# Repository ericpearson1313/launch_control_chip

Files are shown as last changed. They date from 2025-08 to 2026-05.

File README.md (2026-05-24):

# launch_chip
A model rocket launch control chip. A better push button?

## Datasheet
Semiconductors start out as an idea. Early datasheets allow exploration of the functionallity to meet the system need.
I've created a mock datasheet for a launch control chip, to both inspire and try to ground my design as a practical device with multiple applications.
Key functions and parameters set and documented. A compact module was defined which encompassed core functionallity centered around the device. Considering
multiple applications for this module firmed up the I/O to ease integration with clean schematics for each situation. A development board was then designed,
fully integration the LCC into a single board handheld lauch controller, and enabling chip development.

[Datasheet](Launch_chip_arch.pdf)

## Development Board PCB Design
Guided by the datasheet thought process the development board PCB was designed. The KiCad schematic and pcb have been developed and added to the repo.
The design will be revisioned until tapeout release. I'll use this board to bring up the LCC.

[KiCAD Project](dev_board.kicad_pro)

[KiCAD Schematic](dev_board.kicad_sch)

[KiCAD PCB](dev_board.kicad_pcb)

[Bill of Materials](dev_board.csv)

## Datasheet Snapshots

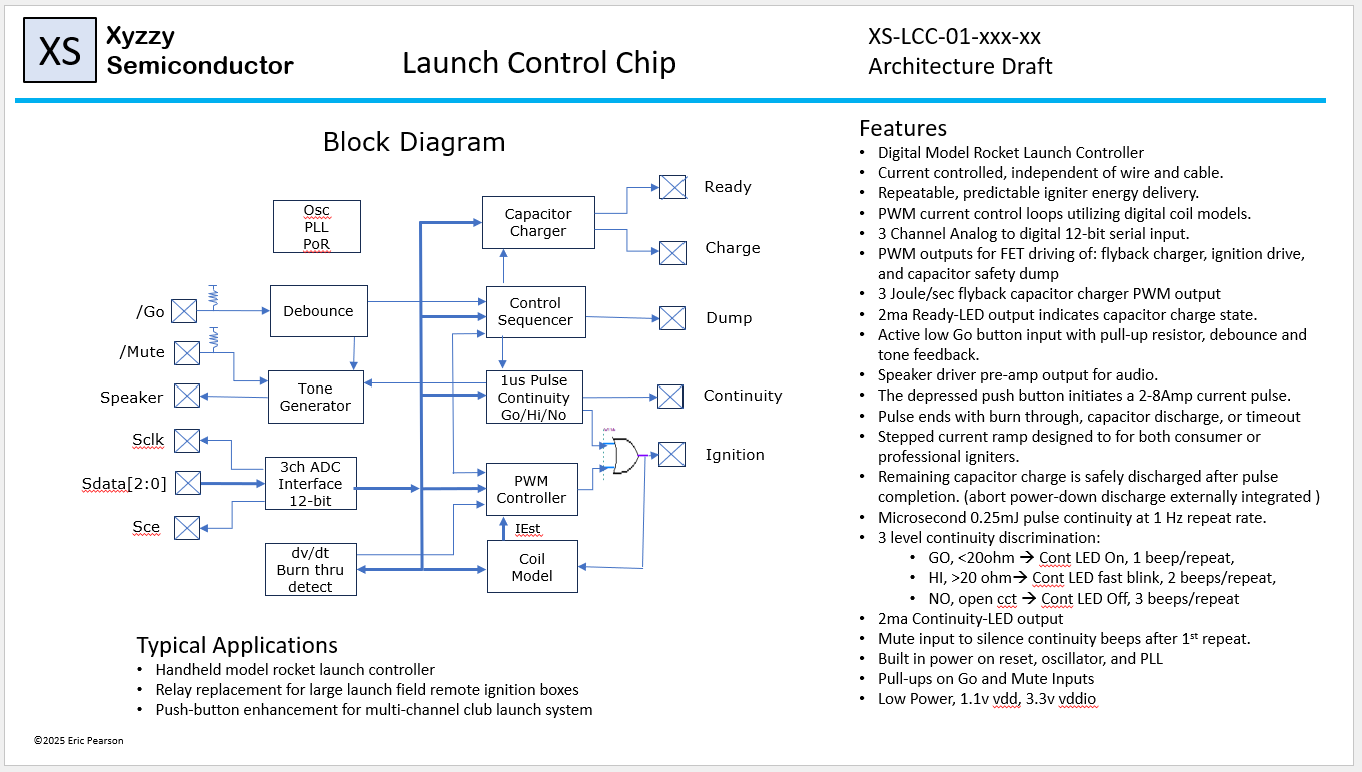
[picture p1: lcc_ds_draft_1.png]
features


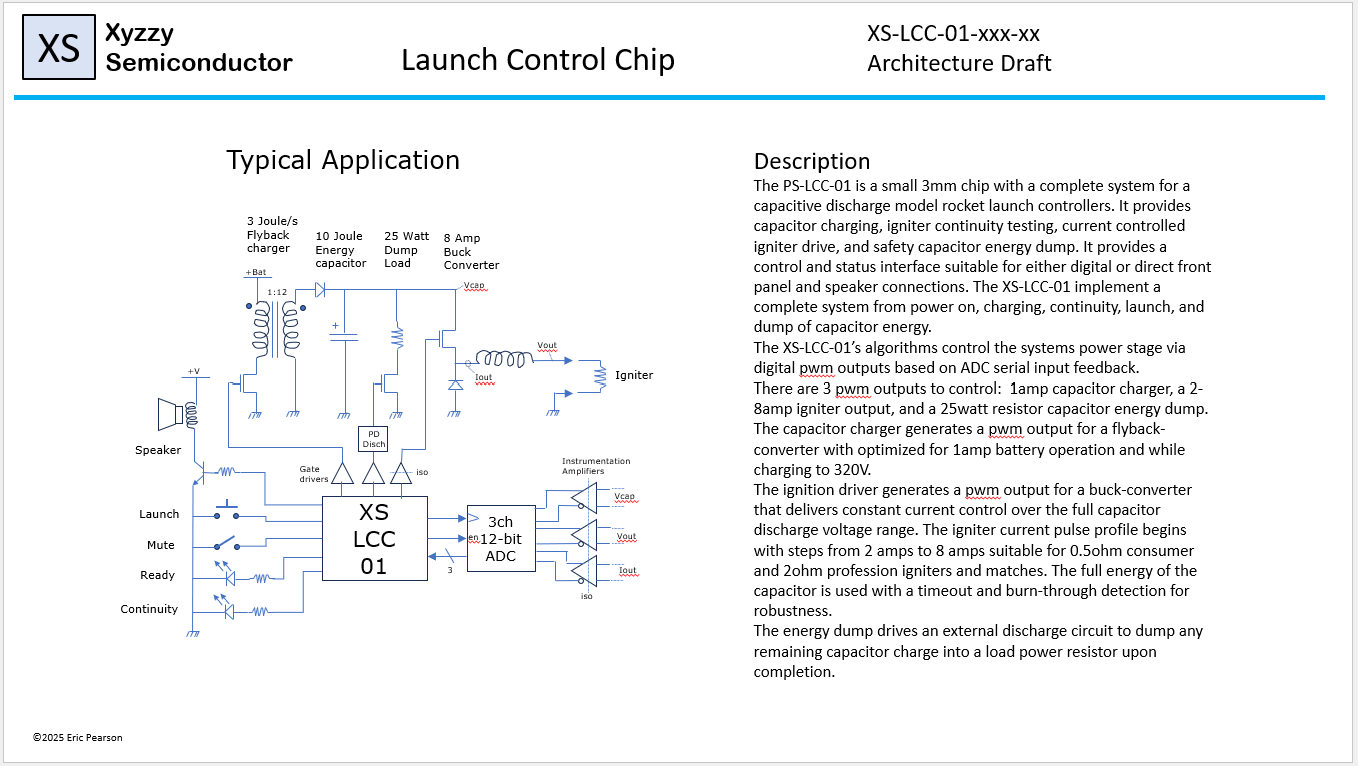
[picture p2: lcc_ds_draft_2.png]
application


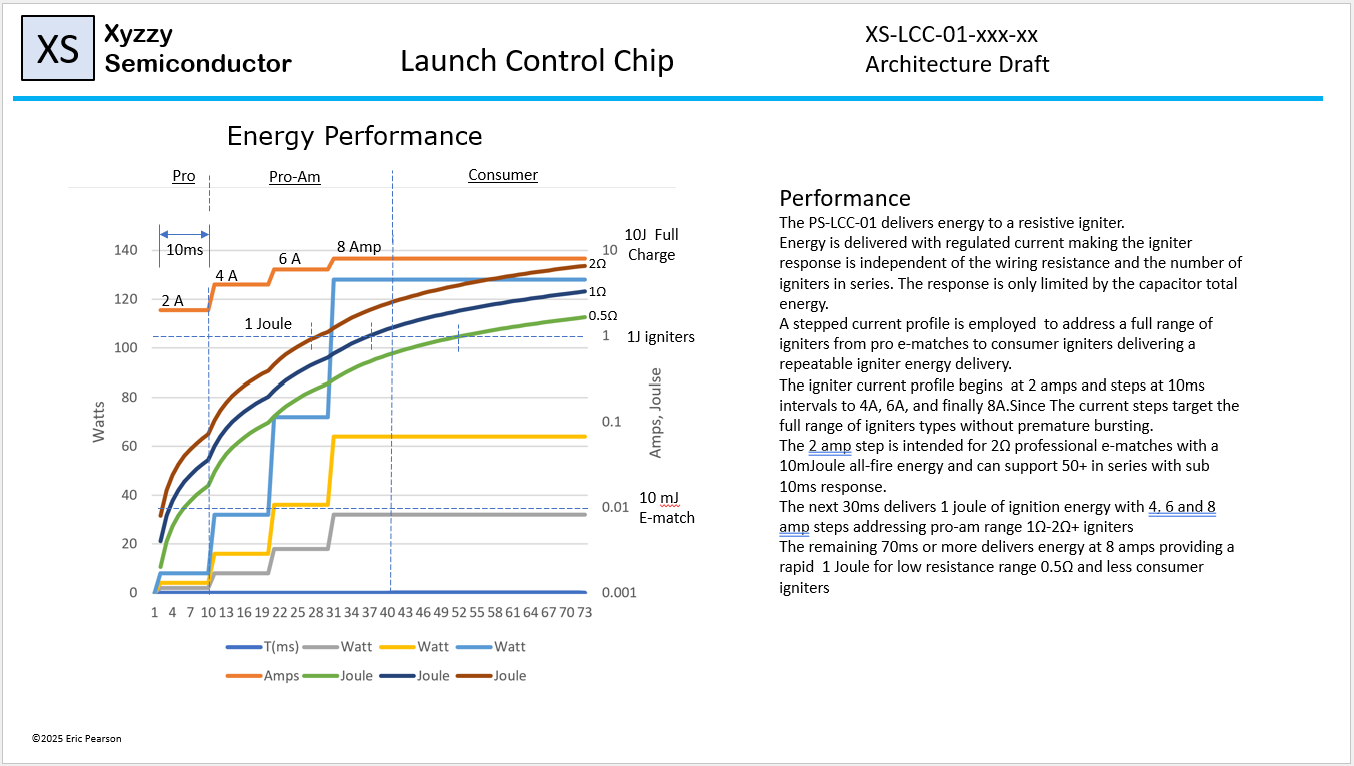
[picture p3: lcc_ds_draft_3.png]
performance


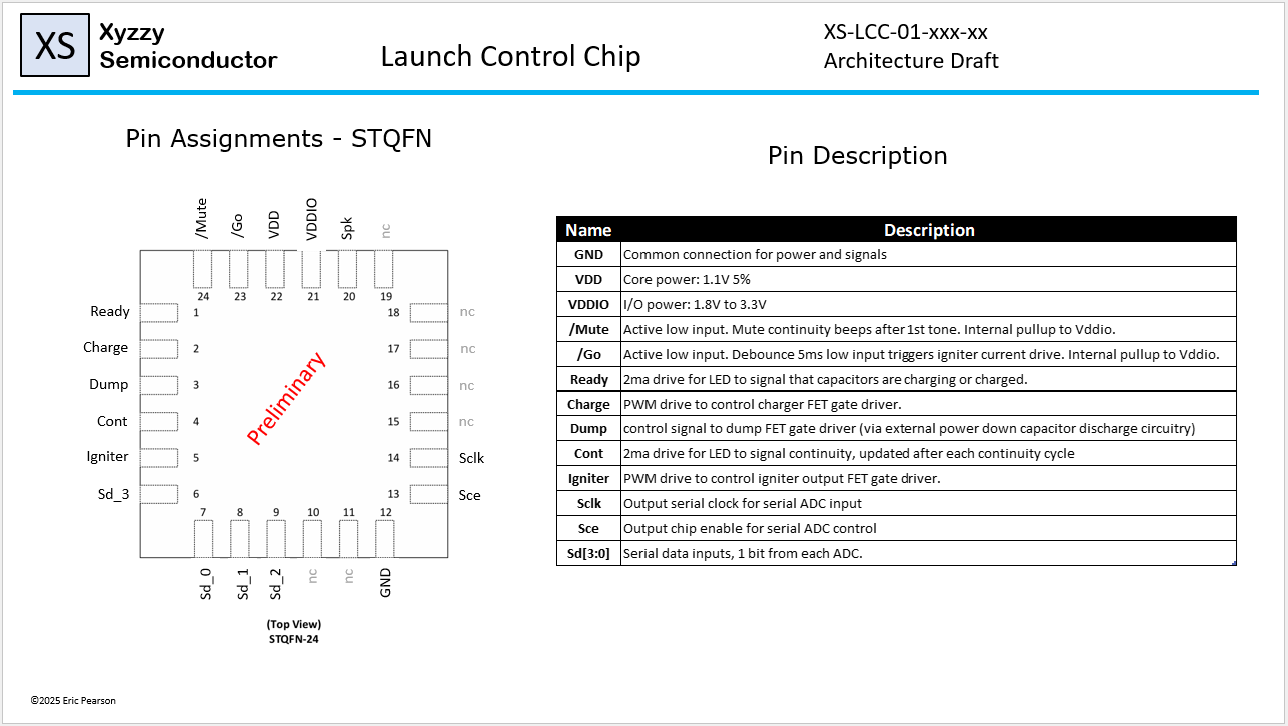
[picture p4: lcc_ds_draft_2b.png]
pinout


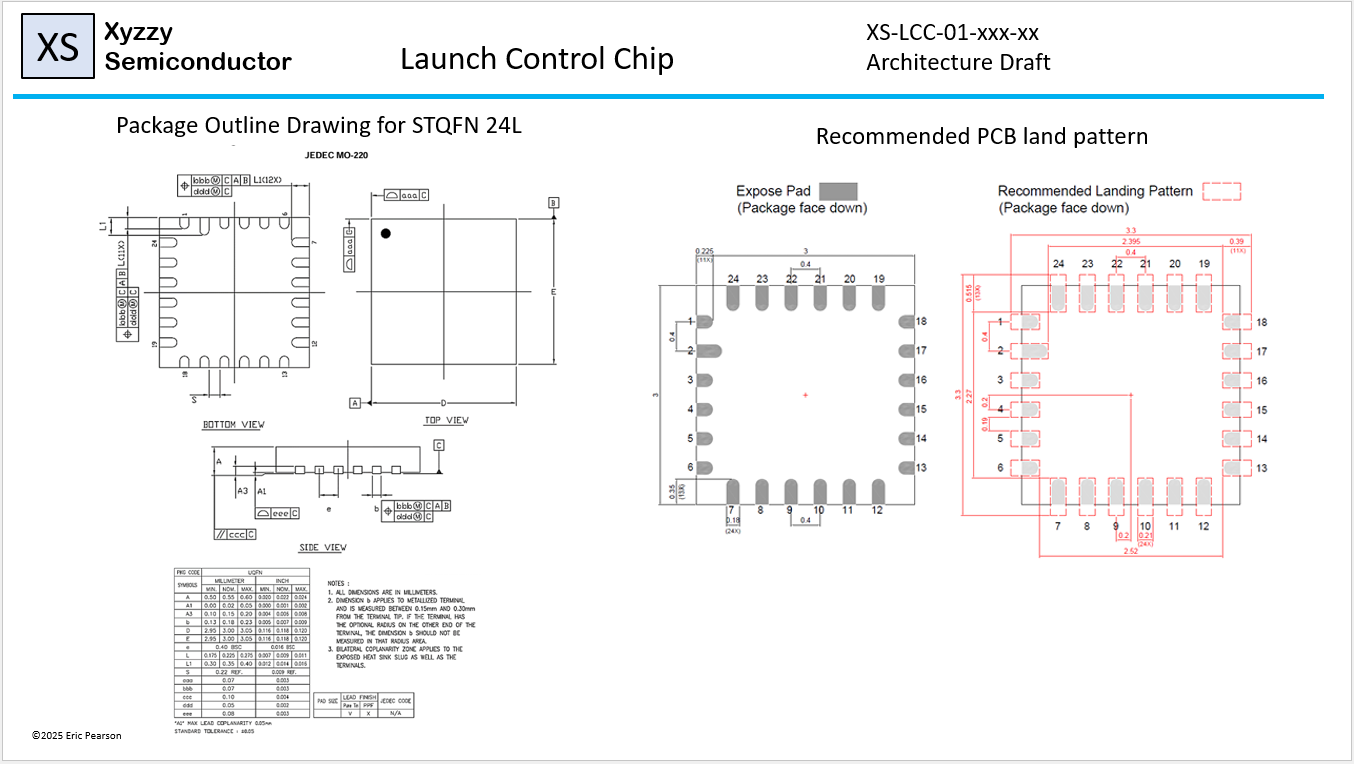
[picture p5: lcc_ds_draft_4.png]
package


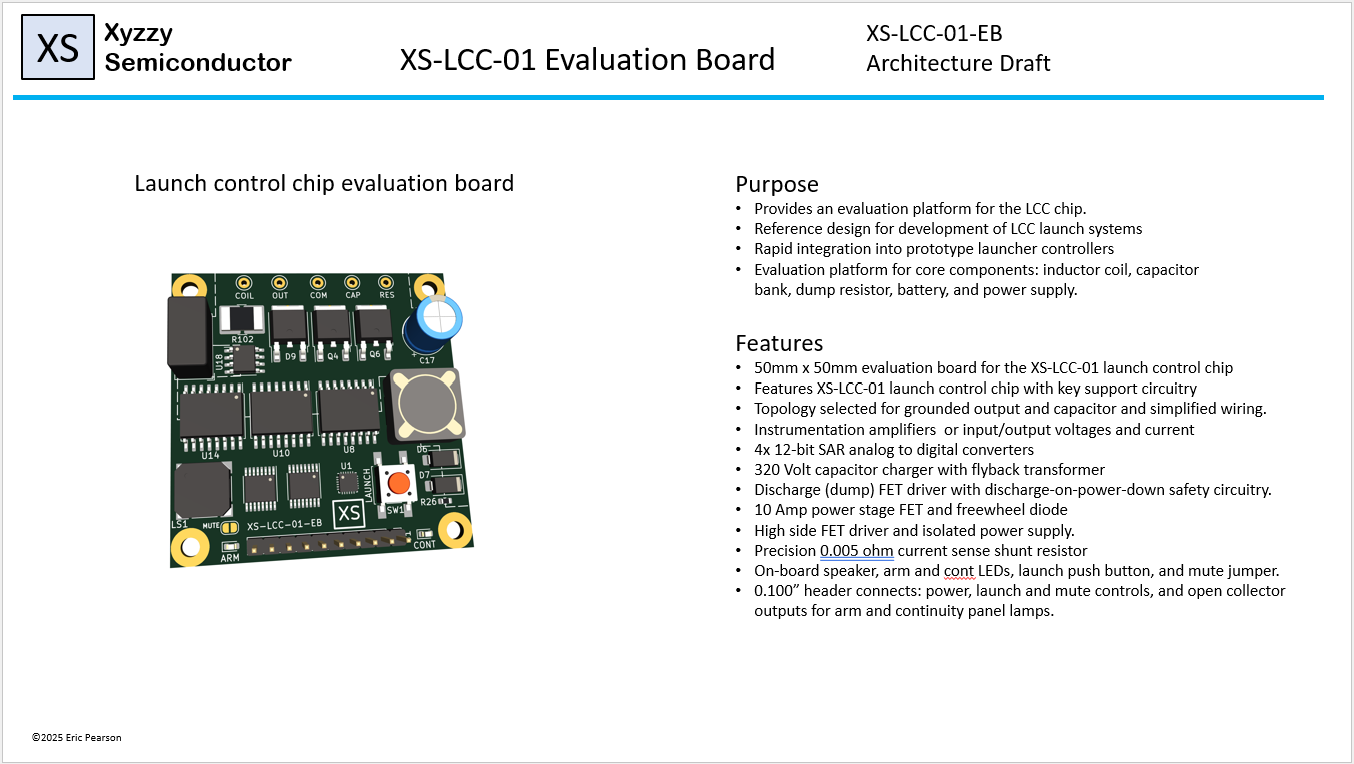
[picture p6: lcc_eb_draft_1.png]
evalboard


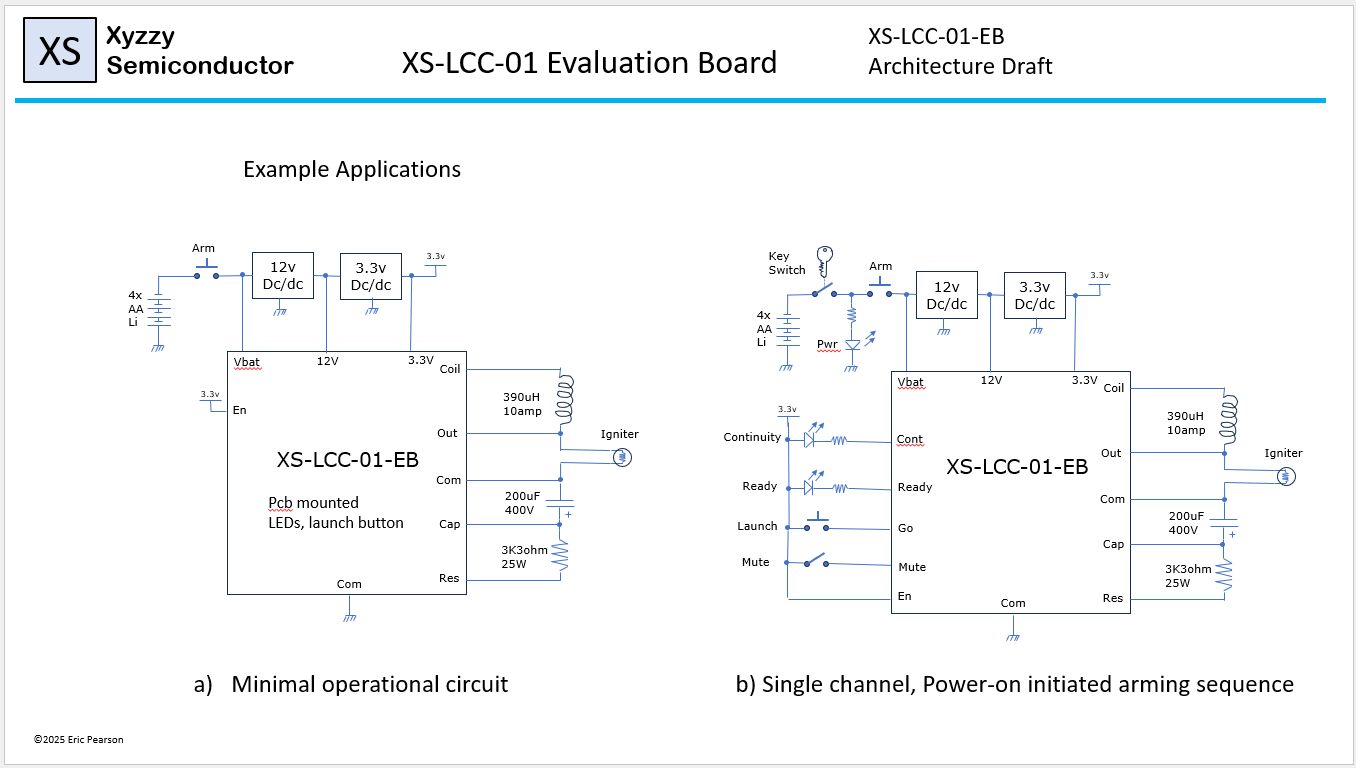
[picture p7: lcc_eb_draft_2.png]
eb_1chan


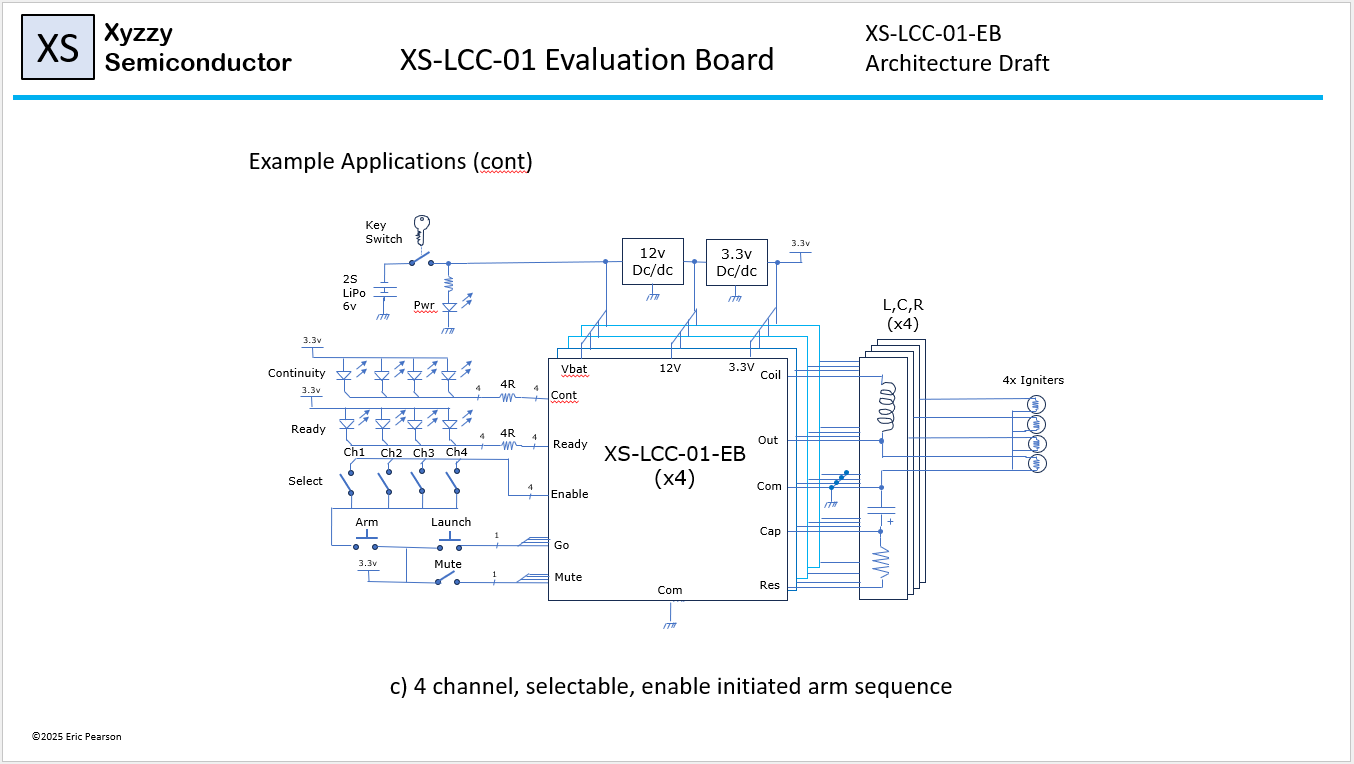
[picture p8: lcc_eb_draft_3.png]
eb_4chan


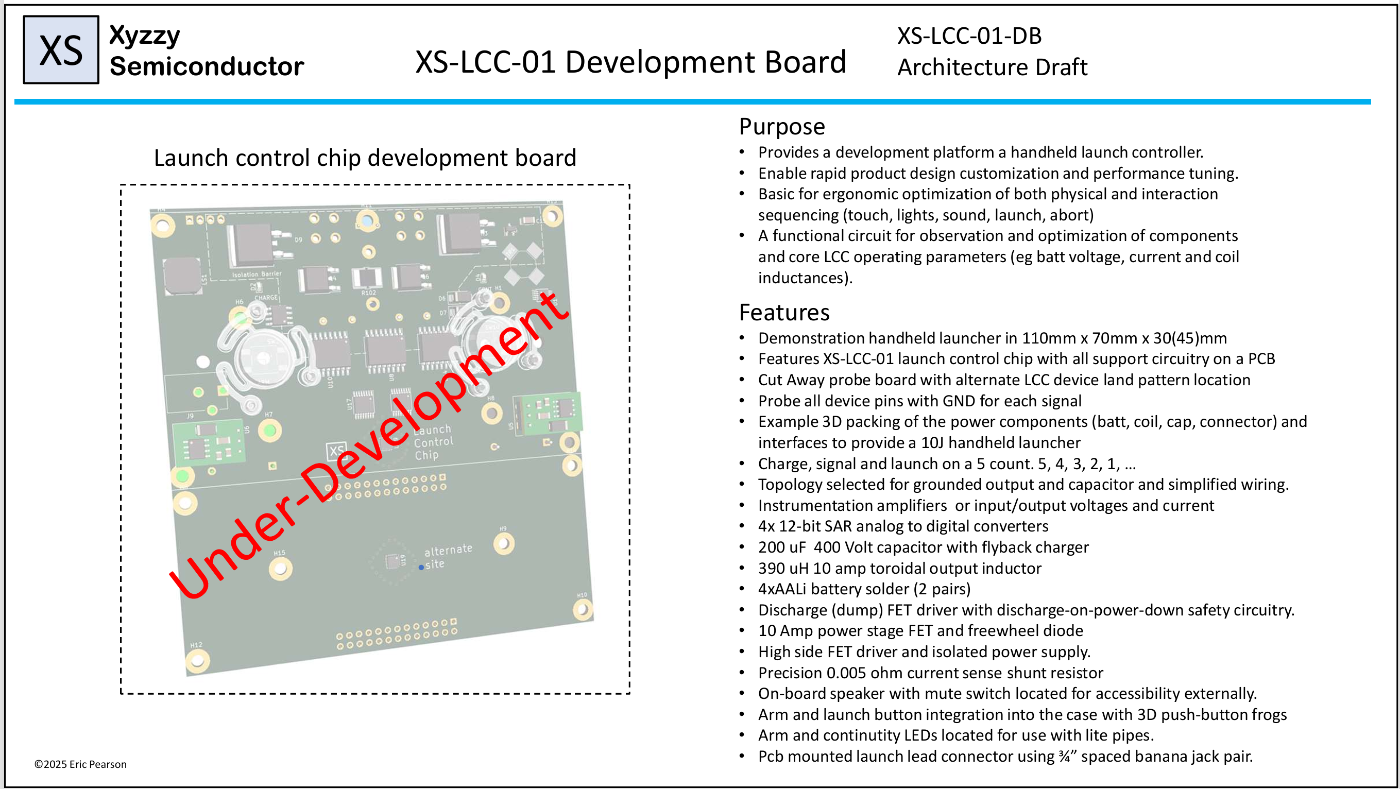
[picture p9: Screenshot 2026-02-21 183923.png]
dev_brd_pre


#### Extra prototype devices 

I have finished development of my 'perfect?' handheld launch controller powered by the launch control chip. Of the prototype run of devices I have a few extra, and have listed them for sale at cost on Ebay for an offer of $35, with free lettermail shipping. If you have followed the same technical direction as myself, I know this chip would have helped me alot, so maybe it could help other similar hobby technical enthusiasts. [LCC-01 Ebay listing](https://www.ebay.ca/itm/157937950540)

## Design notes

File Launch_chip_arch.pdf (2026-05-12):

Osc
PLL
PoR

Coil
Model

PWM
Controller

Ignition

Tone
Generator Speaker | Continuity

Capacitor
Charger

Ready

/Go | Control
Sequencer | Dump

Charge

3ch ADC
Interface
12-bit

Sdata[2:0]

IEst

## Block Diagram

1us Pulse
Continuity
Go/Hi/No

Debounce

dv/dt
Burn thru
detect

/Mute

Sclk

Sce

## Features

- Digital Model Rocket Launch Controller • Current controlled, independent of wire and cable. • Repeatable, predictable igniter energy delivery. • PWM current control loops utilizing digital coil models. • 3 Channel Analog to digital 12-bit serial input. • PWM outputs for FET driving of: flyback charger, ignition drive,

and capacitor safety dump • 3 Joule/sec flyback capacitor charger PWM output • 2ma Ready-LED output indicates capacitor charge state. • Active low Go button input with pull-up resistor, debounce and

tone feedback. • Speaker driver pre-amp output for audio. • The depressed push button initiates a 2-8Amp current pulse. • Pulse ends with burn through, capacitor discharge, or timeout • Stepped current ramp designed to for both consumer or

professional igniters. • Remaining capacitor charge is safely discharged after pulse

completion. (abort power-down discharge externally integrated ) • Microsecond 0.25mJ pulse continuity at 1 Hz repeat rate. • 3 level continuity discrimination: • GO, <20ohm Cont LED On, 1 beep/repeat, • HI, >20 ohm Cont LED fast blink, 2 beeps/repeat, • NO, open cct Cont LED Off, 3 beeps/repeat • 2ma Continuity-LED output • Mute input to silence continuity beeps after 1st repeat. • Built in power on reset, oscillator, and PLL

- Pull-ups on Go and Mute Inputs
- Low Power, 1.1v vdd, 3.3v vddio
- Small size, 3mm x 3mm

## Typical Applications

- Handheld model rocket launch controller • Relay replacement for large launch field remote ignition boxes
- Push-button enhancement for multi-channel club launch system

## Xyzzy

Semiconductor | Launch Control Chip
XS-LCC-01-xxx-xx XS | Architecture Draft

©2025 Eric Pearson

XS

## LCC

01

## +Bat Typical Application

## Xyzzy

# Semiconductor Launch Control Chip

## XS-LCC-01-xxx-xx Architecture Draft 1:12

### 3 Joule/s

Flyback
charger

### 10 Joule

Energy
capacitor

### 25 Watt

Dump
Load

### 8 Amp

Buck
Converter

Igniter

iso Gate drivers

Vcap | Vout Iout Speaker

Launch

Mute

Ready

Continuity

+V

3ch
12-bit
ADC

3

en

iso

Iout Vout Vcap

Instrumentation Amplifiers PD Disch

## Description

The PS-LCC-01 is a small 3mm chip with a complete system for a capacitive discharge model rocket launch controllers. It provides capacitor charging, igniter continuity testing, current controlled igniter drive, and safety capacitor energy dump. It provides a control and status interface suitable for either digital or direct front panel and speaker connections. The XS-LCC-01 implement a complete system from power on, charging, continuity, launch, and dump of capacitor energy.
The XS-LCC-01’s algorithms control the systems power stage via digital pwm outputs based on ADC serial input feedback.
There are 3 pwm outputs to control: 1amp capacitor charger, a 2-8amp igniter output, and a 25watt resistor capacitor energy dump. The capacitor charger generates a pwm output for a flyback-converter with optimized for 1amp battery operation and while charging to 320V.
The ignition driver generates a pwm output for a buck-converter that delivers constant current control over the full capacitor discharge voltage range. The igniter current pulse profile begins with steps from 2 amps to 8 amps suitable for 0.5ohm consumer and 2ohm profession igniters and matches. The full energy of the capacitor is used with a timeout and burn-through detection for robustness.
The energy dump drives an external discharge circuit to dump any remaining capacitor charge into a load power resistor upon completion.

XS

©2025 Eric Pearson

## Xyzzy

# Semiconductor Launch Control Chip

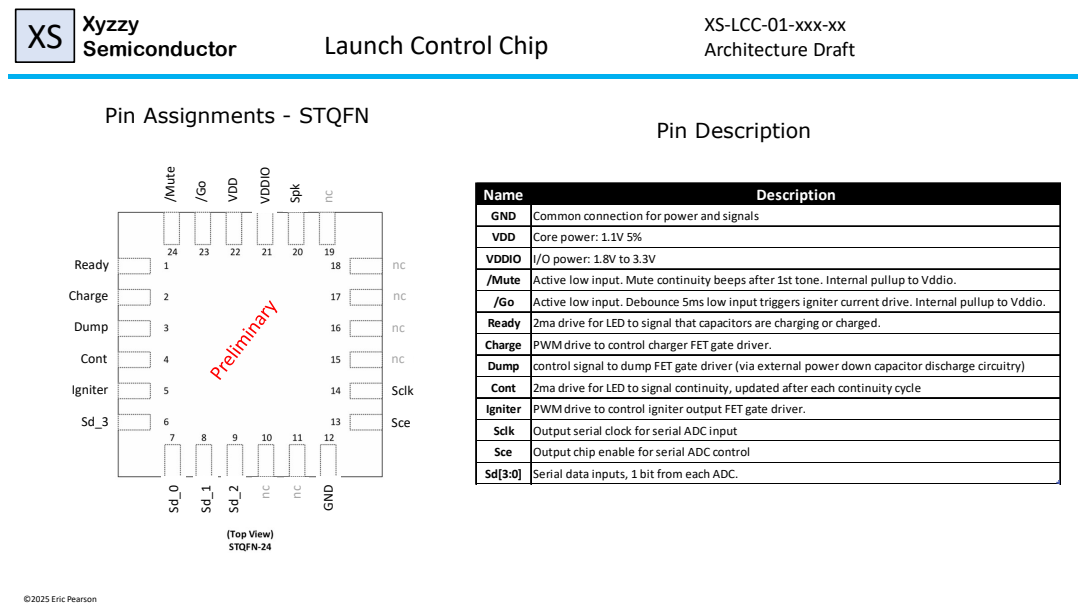
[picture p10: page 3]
XS-LCC-01-xxx-xx XS; Architecture Draft; ©2025 Eric Pearson; VDD; VDDIO; Sclk; Sce; Ready; Charge; Dump; Cont; Igniter; GNDnc; nc /Mute; Spk Sd_0; Pin Description

Pin Assignments - STQFN

Name | Description
GND | Common connection for power and signals
VDD | Core power: 1.1V 5%
VDDIO | I/O power: 1.8V to 3.3V
/Mute | Active low input. Mute continuity beeps after 1st tone. Internal pullup to Vddio.
/Go | Active low input. Debounce 5ms low input triggers igniter current drive. Internal pullup to Vddio.
Ready | 2ma drive for LED to signal that capacitors are charging or charged.
Charge | PWM drive to control charger FET gate driver.
Dump | control signal to dump FET gate driver (via external power down capacitor discharge circuitry)
Cont | 2ma drive for LED to signal continuity, updated after each continuity cycle
Igniter | PWM drive to control igniter output FET gate driver.
Sclk | Output serial clock for serial ADC input
Sce | Output chip enable for serial ADC control
Sd[3:0] | Serial data inputs, 1 bit from each ADC.

## Energy Performance

## Xyzzy

# Semiconductor Launch Control Chip

## XS-LCC-01-xxx-xx Architecture Draft

## Performance

The PS-LCC-01 delivers energy to a resistive igniter.
Energy is delivered with regulated current making the igniter response independent of the wiring resistance and the number of igniters in series. The response is only limited by the capacitor total energy.
A stepped current profile is employed to address a full range of igniters from pro e-matches to consumer igniters delivering a repeatable igniter energy delivery.
The igniter current profile begins at 2 amps and steps at 10ms intervals to 4A, 6A, and finally 8A.Since The current steps target the full range of igniters types without premature bursting.
The 2 amp step is intended for 2Ω professional e-matches with a 10mJoule all-fire energy and can support 50+ in series with sub 10ms response.
The next 30ms delivers 1 joule of ignition energy with 4, 6 and 8 amp steps addressing pro-am range 1Ω-2Ω+ igniters
The remaining 70ms or more delivers energy at 8 amps providing a rapid 1 Joule for low resistance range 0.5Ω and less consumer igniters.

XS

©2025 Eric Pearson

### 2 A

### 4 A

10ms | 6 A

### 8 Amp

### 1 Joule

2Ω
1Ω
0.5Ω
1J igniters

### 10 mJ

E-match

10J Full
Charge
Pro | Pro-Am | Consumer

## Xyzzy

# Semiconductor Launch Control Chip

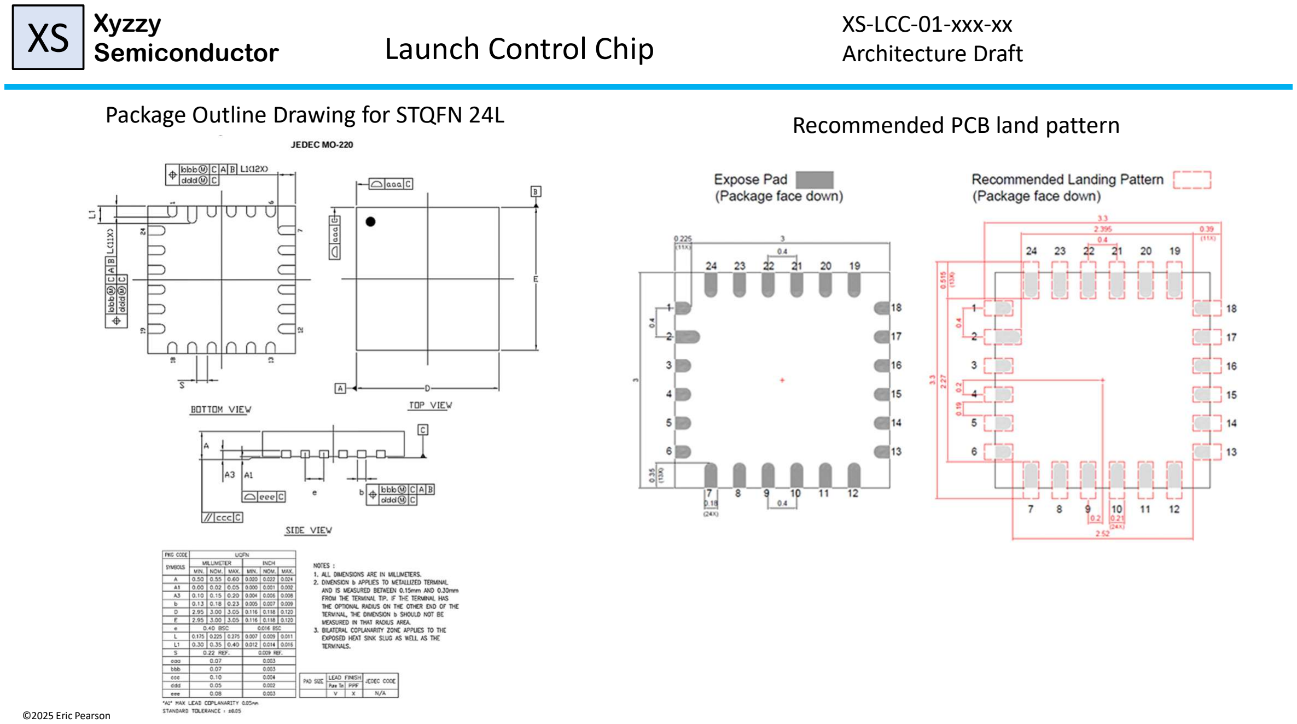
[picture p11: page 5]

## XS-LCC-01-xxx-xx Architecture Draft

## Recommended PCB land pattern

XS

©2025 Eric Pearson

## Package Outline Drawing for STQFN 24L

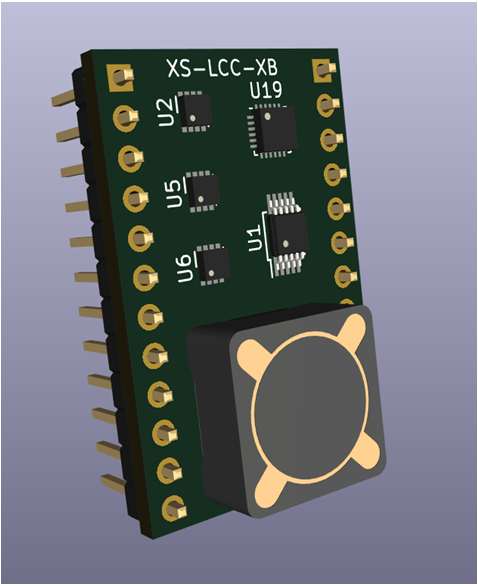
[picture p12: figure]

## Features

- 1.3” x 0.7” engineering board for the XS-LCC launch control chip
- Features XS-LCC-01 launch control chip with core support circuitry
- Integrates the LCC with: • 3x 12bit SAR ADCs with differential inputs
- 1Amp Charger and flyback tranformer • Connection to LCC pins: • for pushbutton, mute inputs
- Leds, and speaker circuits outpus. • Pwm, Dump, and Charge outputs .

## Xyzzy

Semiconductor | XS-LCC-XB Engineering Board
XS-LCC-01-XB XS | Architecture Draft

©2025 Eric Pearson

## Purpose

- Rapid prototyping of capacitory discharge model rocket launcher • Small 3.3v module integrating the core components: LCC, ADCs

and flyback circuit. • 2x12 Pin 0.1” DIP header compatible with prototype boards

## Launch control chip Experimental engineering board

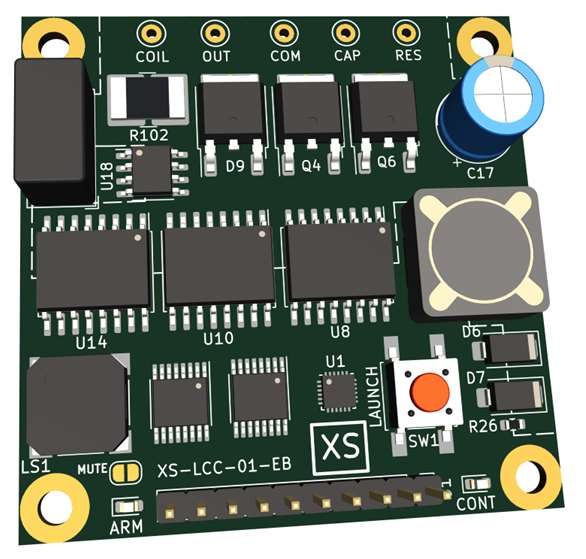
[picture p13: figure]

## Features

- 50mm x 50mm evaluation board for the XS-LCC-01 launch control chip
- Features XS-LCC-01 launch control chip with key support circuitry
- Topology selected for grounded output and capacitor and simplified wiring. • Instrumentation amplifiers or input/output voltages and current • 4x 12-bit SAR analog to digital converters
- 320 Volt capacitor charger with flyback transformer • Discharge (dump) FET driver with discharge-on-power-down safety circuitry. • 10 Amp power stage FET and freewheel diode • High side FET driver and isolated power supply. • Precision 0.005 ohm current sense shunt resistor • On-board speaker, arm and cont LEDs, launch push button, and mute jumper. • 0.100” header connects: power, launch and mute controls, and open collector

outputs for arm and continuity panel lamps.

## Xyzzy

Semiconductor | XS-LCC-01 Evaluation Board
XS-LCC-01-EB XS | Architecture Draft

©2025 Eric Pearson

## Purpose

- Provides an evaluation platform for the LCC chip. • Reference design for development of LCC launch systems
- Rapid integration into prototype launcher controllers
- Evaluation platform for core components: inductor coil, capacitor bank, dump resistor, battery, and power supply.

## Launch control chip evaluation board

## Xyzzy

# Semiconductor XS-LCC-01 Evaluation Board

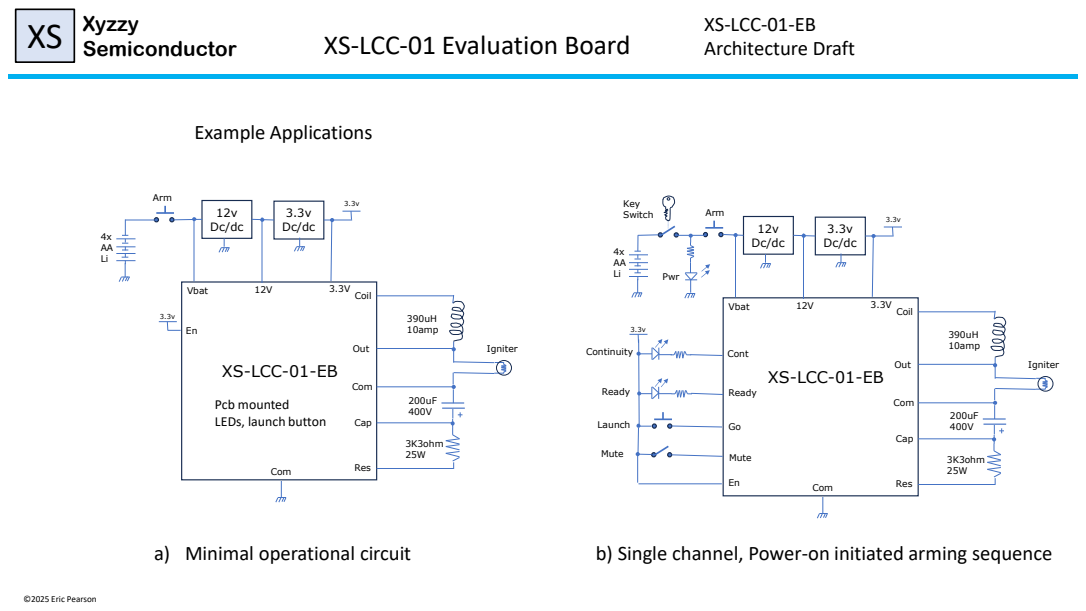
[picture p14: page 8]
XS-LCC-01-EB XS; Architecture Draft; ©2025 Eric Pearson; Example Applications; Igniter; Launch; Mute; Ready; Continuity; Key; Switch; Arm; Coil; Out; Com; Cap; Res; 390uH 10amp; 3K3ohm 25W; Vbat; Pwr 3.3v

Cont
XS-LCC-01-EB

Pcb mounted
LEDs, launch button

a) Minimal operational circuit

b) Single channel, Power-on initiated arming sequence

## Xyzzy

# Semiconductor XS-LCC-01 Evaluation Board

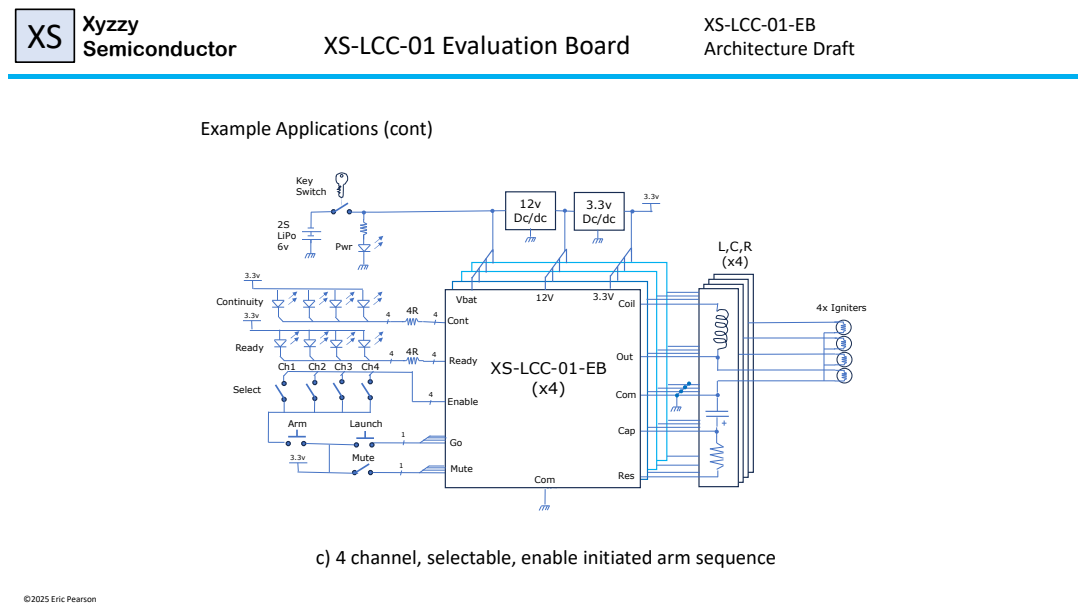
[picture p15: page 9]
XS-LCC-01-EB XS; Architecture Draft; ©2025 Eric Pearson; Mute; Ready; Continuity; Key Switch; 4x Igniters; 2S LiPo; Pwr; 3.3v Arm; XS-LCC-01-EB (x4); Coil; Out; Com; Cap; Res; Vbat; Cont; Enable; Select ³.3v; Launch 3.3v

Example Applications (cont)

c) 4 channel, selectable, enable initiated arm sequence

## Features

- Features XS-LCC-01 launch control chip with all support circuitry
- Showcases packing power components (batt, coil, cap, connector) and all circuitry for a 10J handheld launcher into 110x70x30(45)m
- Cut-away: Probe and Emulator/Analyzer modules for development

## Xyzzy

Semiconductor | XS-LCC-01 Development Board
XS-LCC-01-DB XS | Architecture Draft

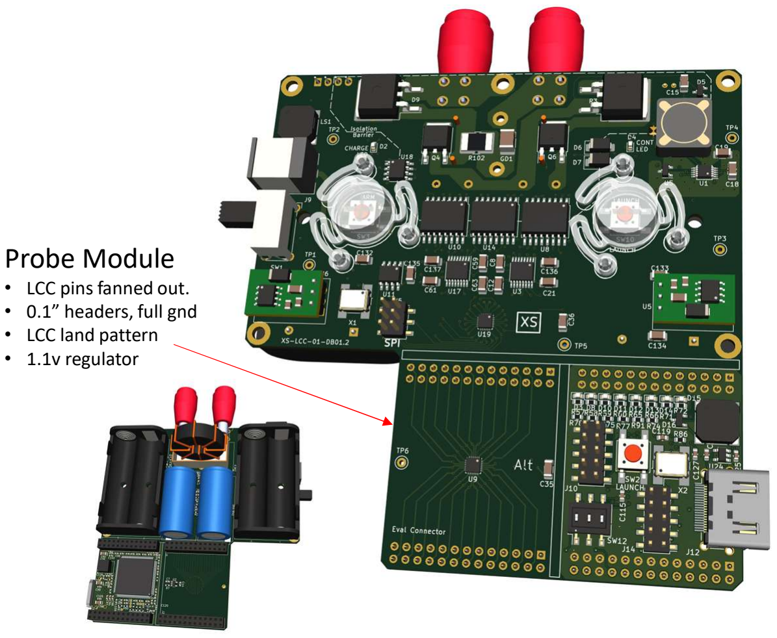
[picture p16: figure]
Probe Module; • LCC land pattern

©2026 Eric Pearson

## Purpose

- Provide a product development platform for the LCC chip. • A functional 10J handheld launch control system for observation,

optimization, and qualification of components, core LCC operating parameters electrical circuitry, packaging and interaction sequencing of touch, light, and sound. • 0.1” Probe header for lab instrumentation and control of LCC signals

- Observe LCC system operation with FPGA emulator/analyzer

## Launch control chip development board

- LCC pins fanned out. • 0.1” headers, full gnd
- 1.1v regulator | FPGA Emulator Analyzer • Altera/Intel Max10 fpga • Sized to enable full emulation of the LCC device • 32 Mbyte SPI8 memory for recording • HDMI connector for display • Fully wired into probe module. • Can be cut away and stacked or run stand alone • Programming and digital I/O connectors • 8 leds, 3 switches, button and speaker

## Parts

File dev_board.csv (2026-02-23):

Reference | Value | Footprint | Datasheet | DPN | JLC | OK | Qty
BT1, BT2 |  | Battery:BatteryHolder_Keystone_2462_2xAA | https://www.digikey.ca/en/products/detail/keystone-electronics/2462/303811 | 36-2462-ND | ~ |  | 2
C1, C3, C5, C7, C10, C11, C14, C16, C20, C26, C28, C32, C34, C40, C45, C50, C66, C70, C75, C91, C98, C104, C115, C125, C126, C128, C129, C141 | 1u | Capacitor_SMD:C_0603_1608Metric | ~ | 399-C0603C105K3RAC7867CT-ND |  |  | 28
C2, C4, C6, C31, C33, C44, C65 | 0.01u | Capacitor_SMD:C_0603_1608Metric | ~ | 399-C0603C103K3RAC7867CT-ND |  |  | 7
C8, C12, C21, C59, C61, C63 | 10u | Capacitor_SMD:C_1206_3216Metric | ~ | 399-C1206C106K4PAC7800CT-ND |  |  | 6
C9, C13, C22, C27, C46, C49, C53, C60, C62, C64, C69, C73, C76, C79, C81-C84, C90, C92-C94, C96, C97, C99-C103, C105, C106, C108-C110, C116, C119-C124, C127, C130, C131, C139, C140, C142-C144 | 0.1u | Capacitor_SMD:C_0603_1608Metric | ~ | 399-C0603C104K3RAC7867CT-ND |  |  | 49
C15 | 0.022u 630v | Capacitor_SMD:C_1206_3216Metric | ~ | 399-13296-1-ND |  |  | 1
C17 | 100u 20v | Capacitor_THT:C_Radial_D5.0mm_H7.0mm_P2.00mm | ~ | 1572-1659-ND |  |  | 1
C18, C19, C35, C36, C51, C52, C58, C132-C137 | 4.7u | Capacitor_SMD:C_1206_3216Metric | ~ | 399-C1206C475K5PAC7800CT-ND |  |  | 13
C23, C37, C47, C48, C71, C74, C77, C78, C80 | 0.001u | Capacitor_SMD:C_0603_1608Metric | ~ | 399-C0603C102K3RAC7867CT-ND |  |  | 9
C24, C25 | 100u 400V | Capacitor_THT:CP_Radial_D16.0mm_P7.50mm | ~ | 400BXW100MEFR18X25 | ~ |  | 2
C29, C30, C38, C39, C54-C57 | 2.2n | Capacitor_SMD:C_0603_1608Metric | ~ | 399-C0603C222K3RAC7867CT-ND |  |  | 8
D1, D16 | BAV99 | Package_TO_SOT_SMD:SOT-23 | https://assets.nexperia.com/documents/data-sheet/BAV99_SER.pdf | BAV99LT1GOSCT-ND |  |  | 2
D2 | ARM | LED_SMD:LED_0603_1608Metric | ~ | 754-2039-1-ND |  |  | 1
D3, D8, D10-D15 | Yel | LED_SMD:LED_0603_1608Metric |  | 754-2039-1-ND |  |  | 8
D4 | CONT | LED_SMD:LED_0603_1608Metric | ~ | 754-2039-1-ND |  |  | 1
D5 | GSD2004S | Package_TO_SOT_SMD:SOT-23 | https://jlcpcb.com/partdetail/DiodesIncorporated-MMBD3004S_7F/C85606 | GSD2004S-E3-08CT-ND | C85606 |  | 1
D6, D7 | ES1J | Diode_SMD:D_SMA | https://jlcpcb.com/partdetail/st_semtech-ES1JD/C99410 | 1655-ES1JCT-ND | C99410 |  | 2
D9 | ‎STPSC10065G2 | Package_TO_SOT_SMD:TO-263-2_TabPin1 | https://jlcpcb.com/partdetail/WeenSemiconductors-NXPSC10650B6J/C602663 | 497-STPSC10065G2-TRCT-ND | C602663 |  | 1
FB2-FB8 | Ferrite | Inductor_SMD:L_0603_1608Metric | -- mixed values -- | 490-5254-1-ND |  |  | 7
FR1, FR2 |  | myspace pcb:button_frog | ~ | ~ |  |  | 2
GD1 | GDT 500V | Capacitor_SMD:C_1812_4532Metric_Pad1.57x3.40mm_HandSolder | https://www.digikey.ca/en/products/detail/littelfuse-inc/SG500Q/4286095 | F11278CT-ND |  |  | 1
H1-H4, H9 |  | MountingHole:MountingHole_3mm_Pad | ~ | ~ |  |  | 5
J1-J3, J6 | Conn_02x13_Odd_Even | Connector_PinSocket_2.54mm:PinSocket_2x13_P2.54mm_Vertical | https://www.digikey.ca/en/products/detail/samtec-inc/ESW-113-12-T-D/7207386 | ESW-113-12-T-D-ND |  |  | 4
J4 | Jack(Red) | myspace pcb:CalTest_CT3151 | https://www.digikey.ca/en/products/detail/cal-test-electronics/CT3151-0/6005441 | BKCT3151-2-ND |  |  | 1
J5 | Conn_01x06 | Connector_PinHeader_2.54mm:PinHeader_2x03_P2.54mm_Vertical | https://www.digikey.ca/en/products/detail/harwin-inc/M20-8760342/3727889 | 952-1922-ND |  |  | 1
J7 | Jack(Black) | myspace pcb:CalTest_CT3151 | https://www.digikey.ca/en/products/detail/cal-test-electronics/CT3151-0/6005441 | BKCT3151-0-ND |  |  | 1
J9 | Barrel_Jack | Connector_BarrelJack:BarrelJack_CUI_PJ-063AH_Horizontal | https://www.digikey.ca/en/products/detail/same-sky-formerly-cui-devices/PJ-063AH/2161208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 | CP-063AH-ND |  |  | 1
J10, J14 | Conn_02x05_Odd_Even | Connector_PinHeader_2.54mm:PinHeader_2x05_P2.54mm_Vertical | ~ | 732-2672-ND |  |  | 2
J12 | HDMI_D_1.4 | Connector_HDMI:HDMI_A_Amphenol_10029449-x01xLF_Horizontal | https://www.digikey.ca/en/products/detail/amphenol-cs-fci/10029449-111RLF/2785386 | 609-4614-1-ND |  |  | 1
L1 | 390uH 5A | Inductor_THT:L_Toroid_Vertical_L35.6mm_W17.8mm_P12.70mm_Pulse_E | https://www.digikey.ca/en/products/detail/signal-transformer/HCTI-390-5-0/7362986 | 595-1735-ND | ~ |  | 1
LS1, LS2 | Speaker | Buzzer_Beeper:PUIAudio_SMT_0825_S_4_R | https://www.digikey.ca/en/products/detail/pui-audio-inc/smt-0825-s-4-r/1464807 | 668-1068-1-ND |  |  | 2
PS1 | RM-1212S | Converter_DCDC:Converter_DCDC_Murata_MEE1SxxxxSC_THT | https://power.murata.com/pub/data/power/ncl/kdc_mee1.pdf | 945-1209-ND |  |  | 1
Q1 | STR2P3LLH6(Pfet) | Package_TO_SOT_SMD:SOT-23 | https://jlcpcb.com/partdetail/TechPublic-PMV48XP/C2959854 | 497-15520-1-ND |  |  | 1
Q2, Q3, Q7, Q9, Q10 | MMBT3904 | Package_TO_SOT_SMD:SOT-23 | https://www.onsemi.com/pub/Collateral/2N3903-D.PDF | 4530-MMBT3904CT-ND |  |  | 5
Q4, Q6 | IPD60R145 | Package_TO_SOT_SMD:TO-252-2 | https://www.digikey.ca/en/products/detail/infineon-technologies/IPD60R145CFD7ATMA1/8627180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 | 448-IPD60R145CFD7ATMA1CT-ND | C3277918 | OK | 2
Q5 | IRLML0060TRPBF | Package_TO_SOT_SMD:SOT-23 | https://www.digikey.ca/en/products/detail/infineon-technologies/IRLML0060TRPBF/2202213 | IRLML0060TRPBFCT-ND | C3277918 | OK | 1
R1, R2, R29 | 100K | Resistor_SMD:R_0603_1608Metric | https://jlcpcb.com/partdetail/VikingTech-AR03DTCX1003/C319967 | RMCF0603FT100KCT-ND | C319967 |  | 3
R3 | 3K3 25W | Package_TO_SOT_SMD:TO-263-2_TabPin1 | https://www.digikey.ca/en/products/detail/bourns-inc/PWR263S-20-3301F/2043980 | 118-PWR263S-20-3301F-ND | C4271625 | OK | 1
R4, R6, R7, R9-R12, R14, R43, R53, R74-R76, R78, R83, R98, R101 | 10K | Resistor_SMD:R_0603_1608Metric | -- mixed values -- | 311-10.0KHRCT-ND | -- mixed values -- |  | 17
R5, R22, R33, R34 | 10R | Resistor_SMD:R_0603_1608Metric | https://jlcpcb.com/partdetail/827060-HP03W5F200KT5E/C778416 | P10.0HCT-ND | C778416 |  | 4
R8 | 2K | Resistor_SMD:R_0603_1608Metric | https://jlcpcb.com/partdetail/VikingTech-AR03DTCX2001/C319700 | P2.00KHCT-ND | C319700 |  | 1
R13 | 51.1K | Resistor_SMD:R_0603_1608Metric | https://jlcpcb.com/partdetail/VikingTech-AR03FTC5112/C234563 | P51.1KDBCT-ND | C234563 |  | 1
R15, R31, R46, R57-R60, R65, R66, R71-R73, R77, R108 | 1K | Resistor_SMD:R_0603_1608Metric | https://jlcpcb.com/partdetail/VikingTech-AR03DTCX1003/C319967 | P1.00KHCT-ND | C319967 |  | 14
R16-R19, R23, R47, R48, R50, R54, R67-R70, R86, R87, R91, R105 | 22R | Resistor_SMD:R_0603_1608Metric | https://jlcpcb.com/partdetail/VikingTech-AR03DTCX1003/C319967 | P22.0HCT-ND | -- mixed values -- |  | 17
R20, R21, R80, R81 | 1.99M | Resistor_SMD:R_0603_1608Metric | https://jlcpcb.com/partdetail/827060-HP03W5F200KT5E/C778416 | 541-MCT0603MD2004BP500CT-ND | C778416 |  | 4
R24, R26, R49, R51, R55, R56, R84, R90, R97, R99, R103, R104, R110 | 0R | Resistor_SMD:R_0603_1608Metric | -- mixed values -- | P0.0GCT-ND | -- mixed values -- |  | 13
R25, R28, R82 | 10.01K | Resistor_SMD:R_0603_1608Metric | https://jlcpcb.com/partdetail/827060-HP03W5F200KT5E/C778416 | 10-ERA-3VRW1002VCT-ND | C778416 |  | 3
R27 | 1.001K | Resistor_SMD:R_0603_1608Metric | https://jlcpcb.com/partdetail/827060-HP03W5F200KT5E/C778416 | 10-ERA-3VRW1001VCT-ND | C778416 |  | 1
R30, R52, R79 | 47K | Resistor_SMD:R_0603_1608Metric | https://jlcpcb.com/partdetail/827060-HP03W5F200KT5E/C778416 | P47KGCT-ND | C778416 |  | 3
R32, R37, R38, R41, R42, R45 | np | Resistor_SMD:R_0603_1608Metric |  | ~ |  |  | 6
R35, R36, R39, R40, R61-R64 | 51R | Resistor_SMD:R_0603_1608Metric | https://jlcpcb.com/partdetail/827060-HP03W5F200KT5E/C778416 | P51.0HCT-ND | C778416 |  | 8
R44 | 3k3 | Resistor_SMD:R_0603_1608Metric | https://jlcpcb.com/partdetail/VikingTech-AR03DTCX1003/C319967 | 311-3.30KHRCT-ND | C319967 |  | 1
R88 | DNI | Resistor_SMD:R_0603_1608Metric | https://jlcpcb.com/partdetail/Panasonic-ERJUP3F1002V/C491211 | ~ | C491211 |  | 1
R102 | 0.005R 1W | myspace pcb:R_2818 current sense | https://www.digikey.ca/en/products/detail/vishay-dale/WSHP28185L000FEA/6605230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 | 846-GMR320HJAAFD5L00CT-ND |  | OK | 1
SW1 | SW_SPST | Button_Switch_THT:SW_E-Switch_EG1224_SPDT_Angled | https://www.digikey.ca/en/products/detail/e-switch/EG1224/502052?s=N4IgTCBcDaIKIHECMYwBYQF0C%2BQ | EG2585-ND |  |  | 1
SW2, SW10 | LAUNCH | myspace pcb:SW_SPST_HP03 | https://www.digikey.ca/en/products/detail/nkk-switches/HP0315AFKP2-R/1242035 | 360-2595-1-ND |  |  | 2
SW3 | ARM | myspace pcb:SW_SPST_HP03 | https://www.digikey.ca/en/products/detail/nkk-switches/HP0315AFKP2-R/1242035 | 360-2595-1-ND |  |  | 1
SW12 | SW_DIP_x03 | Button_Switch_SMD:SW_DIP_SPSTx03_Slide_Omron_A6S-310x_W8.9mm_P2.54mm | ~ | CT2193LPST-ND |  |  | 1
TP1-TP7, TP9-TP13, TP15 |  | -- mixed values -- | -- mixed values -- | 36-1037-ND |  |  | 13
TR1 | PA0367A | myspace pcb:PA0637A Pulse Coil 3D | https://mm.digikey.com/Volume0/opasdata/d220001/medias/docus/4819/PA0367A.pdf | 553-1978-1-ND | C5382098 |  | 1
U1 | LT3420 | Package_SO:MSOP-10_3x3mm_P0.5mm | https://jlcpcb.com/partdetail/AnalogDevices-LT3420EMSPBF/C670531 | LT3420EMS#PBF-ND | C670531 |  | 1
U2, U12, U24 | TLV74318 | Package_TO_SOT_SMD:SOT-23-5 | https://www.ti.com/lit/ds/symlink/tlv743p.pdf | 296-48712-1-ND |  |  | 3
U3, U17 | AD7352 | Package_SO:TSSOP-16_4.4x5mm_P0.65mm | https://www.analog.com/media/en/technical-documentation/data-sheets/AD7352.pdf | AD7352YRUZ-ND |  |  | 2
U4, U23 | TLV74325 | Package_TO_SOT_SMD:SOT-23-5 | https://www.ti.com/lit/ds/symlink/tlv743p.pdf | 296-48989-1-ND |  |  | 2
U5 | LMO78_03-1.0 | Converter_DCDC:Converter_DCDC_Murata_OKI-78SR_Horizontal | https://www.digikey.ca/en/products/detail/gaptec-electronic/LMO78-03-1-0/13691989 | 3182-LMO78_03-1.0-ND | ~ |  | 1
U6 | 4945 | Converter_DCDC:Converter_DCDC_Murata_OKI-78SR_Horizontal | https://www.pololu.com/product/4945 | 2183-4945-ND | ~ |  | 1
U7 | MCP1416 | Package_TO_SOT_SMD:SOT-23-5 | http://ww1.microchip.com/downloads/en/DeviceDoc/20002092F.pdf | MCP1416T-E/OTCT-ND |  |  | 1
U8, U10 | AMC3330 | Package_SO:SOIC-16W_7.5x10.3mm_P1.27mm | https://www.ti.com/lit/ds/symlink/amc3330.pdf | 296-AMC3330DWE-ND |  |  | 2
U9, U19 | XS-LCC-01 | myspace pcb:QFN-24-3x3mm | https://github.com/ericpearson1313/launch_control_chip | ~ |  |  | 2
U11 | AT25xxx | Package_SO:SOIC-8_3.9x4.9mm_P1.27mm | https://www.renesas.com/en/document/dst/at25eu0011a-datasheet?r=1608521 | 1695-AT25EU0011A-SSHN-TCT-ND |  |  | 1
U13, U22 | LM809 | Package_TO_SOT_SMD:SOT-23 | http://www.ti.com/lit/ds/symlink/lm809.pdf | LM809M3-2.63/NOPBCT-ND |  |  | 2
U14 | AMC3302 | Package_SO:SOIC-16W_7.5x10.3mm_P1.27mm | https://www.ti.com/lit/ds/symlink/amc3302.pdf | 296-AMC3302DWERCT-ND |  |  | 1
U18 | IR2127 | Package_SO:SOIC-8_3.9x4.9mm_P1.27mm | https://jlcpcb.com/partdetail/InfineonTechnologies-IR2127STRPBF/C371089 | IR2127SPBFCT-ND | C356723 |  | 1
U20 | MAX10M04 | Package_QFP:EQFP-144-1EP_20x20mm_P0.5mm_EP8.93x8.7mm_ThermalVias |  | 544-3054-ND |  |  | 1
U25 | S80KS2563GABHV020 | myspace pcb:FBGA-24_6mmx8mm_Layout5x5_P1.00mm | https://www.infineon.com/dgdl/Infineon-S80KS2563_1.8_V_256-Mb_Octal_xSPI_Interface_HyperRAM_(Self-Refresh_DRAM)-DataSheet-v01_00-EN.pdf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 | 448-S80KS2563GABHV020-ND |  |  | 1
X1, X2 | ASE-48MHz | Oscillator:Oscillator_SMD_Abracon_ASV-4Pin_7.0x5.1mm_HandSoldering | http://www.abracon.com/Oscillators/ASV.pdf | 535-9328-1-ND |  |  | 2

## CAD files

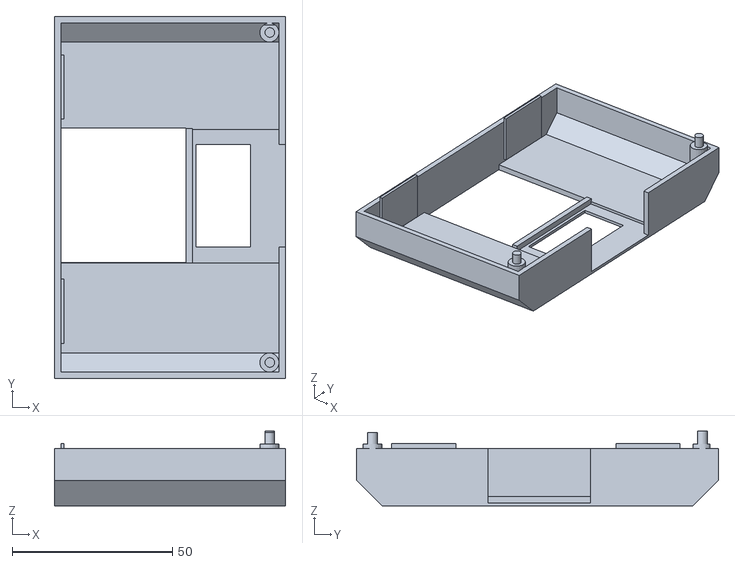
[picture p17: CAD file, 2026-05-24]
3D/lcc enclosure bot v1_0.stl
72.1 x 113.0 x 23.4

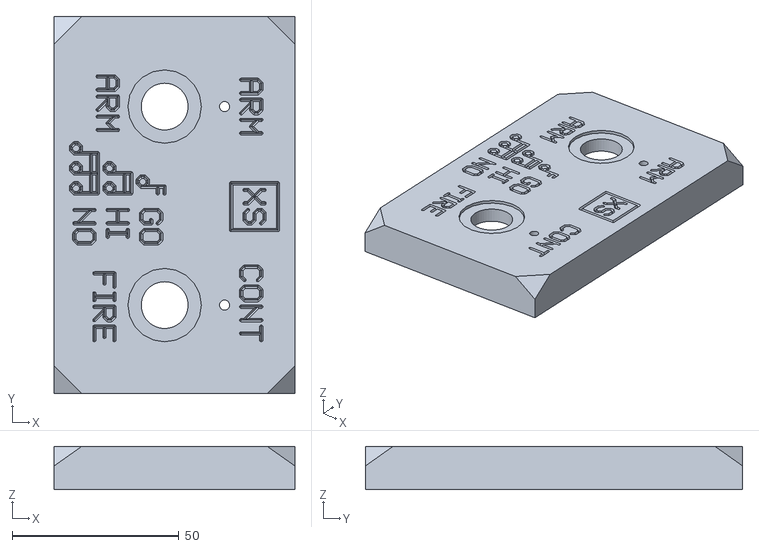
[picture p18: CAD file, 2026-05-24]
3D/lcc enclosure top v1_5.stl
72.1 x 113.0 x 13.0

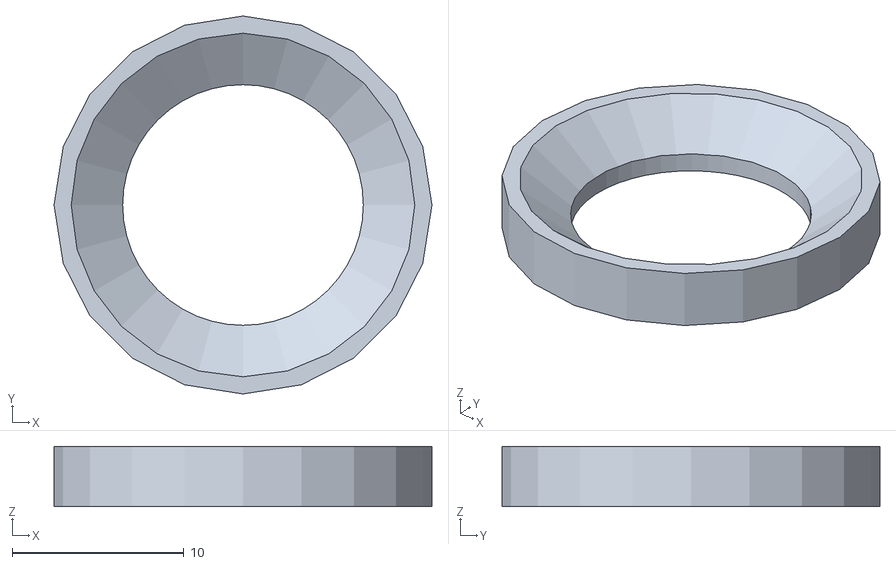
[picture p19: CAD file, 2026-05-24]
3D/lcc button ring v1_1.stl
22.0 x 22.0 x 3.50

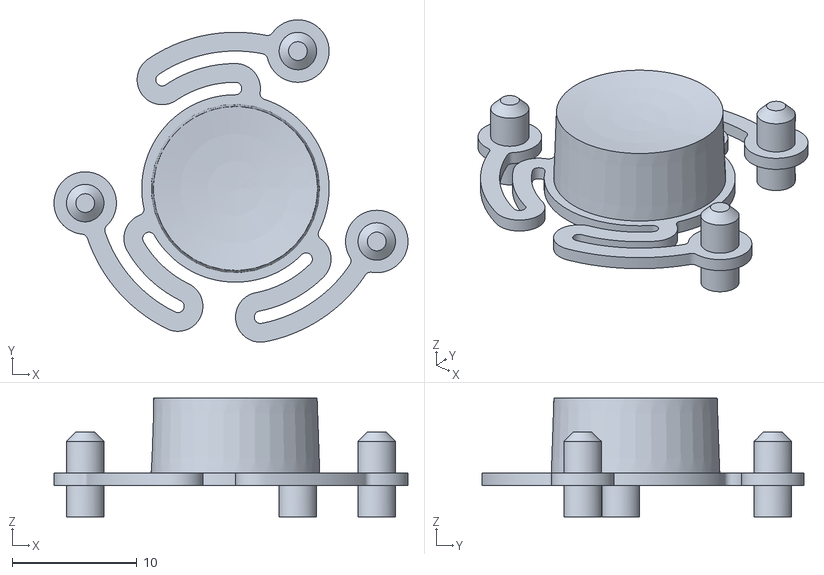
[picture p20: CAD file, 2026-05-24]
3D/button.stp.stl
28.3 x 25.8 x 9.50

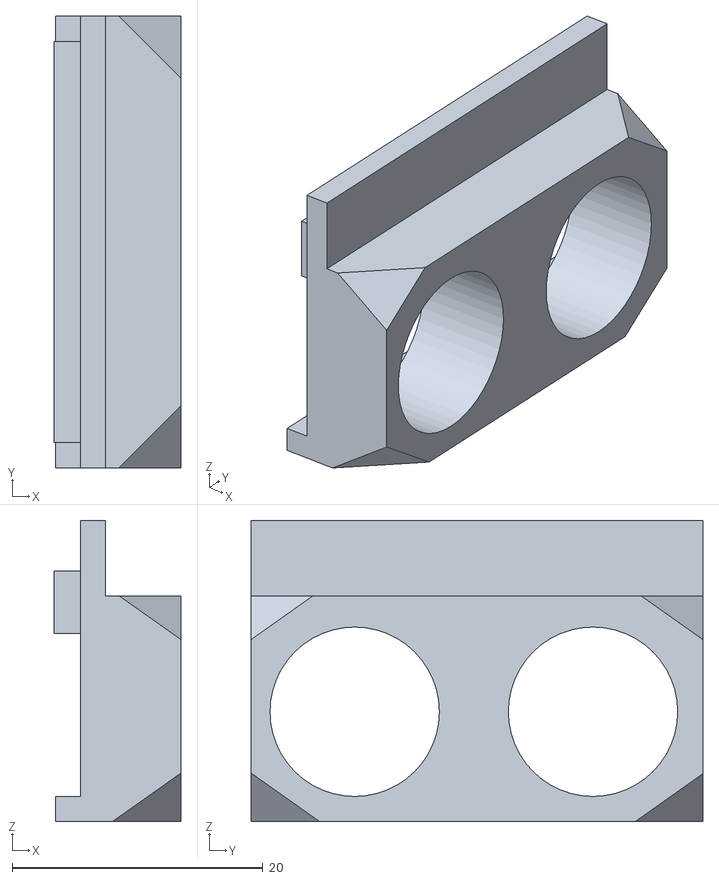
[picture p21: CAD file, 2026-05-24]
3D/lcc term cov v1_0.stl
10.1 x 36.0 x 24.0

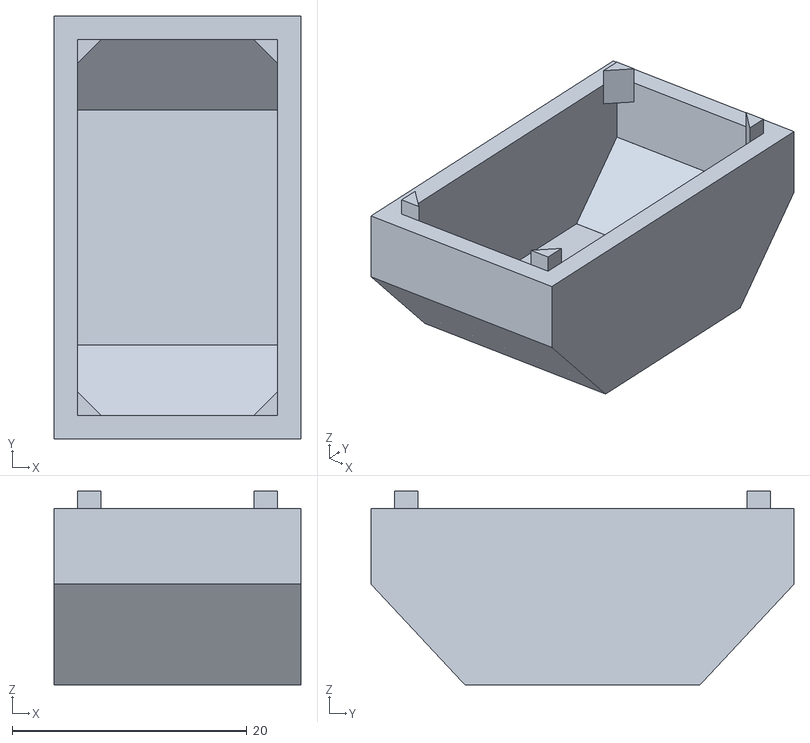
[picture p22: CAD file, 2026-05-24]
3D/lcc coil cov v1_5.stl
21.0 x 36.0 x 16.5

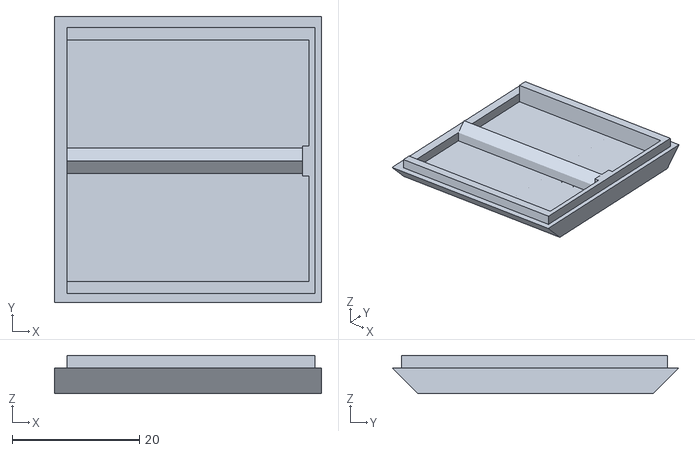
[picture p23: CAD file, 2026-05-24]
3D/lcc enclosure bot plate v1_5.stl
42.0 x 45.0 x 6.00

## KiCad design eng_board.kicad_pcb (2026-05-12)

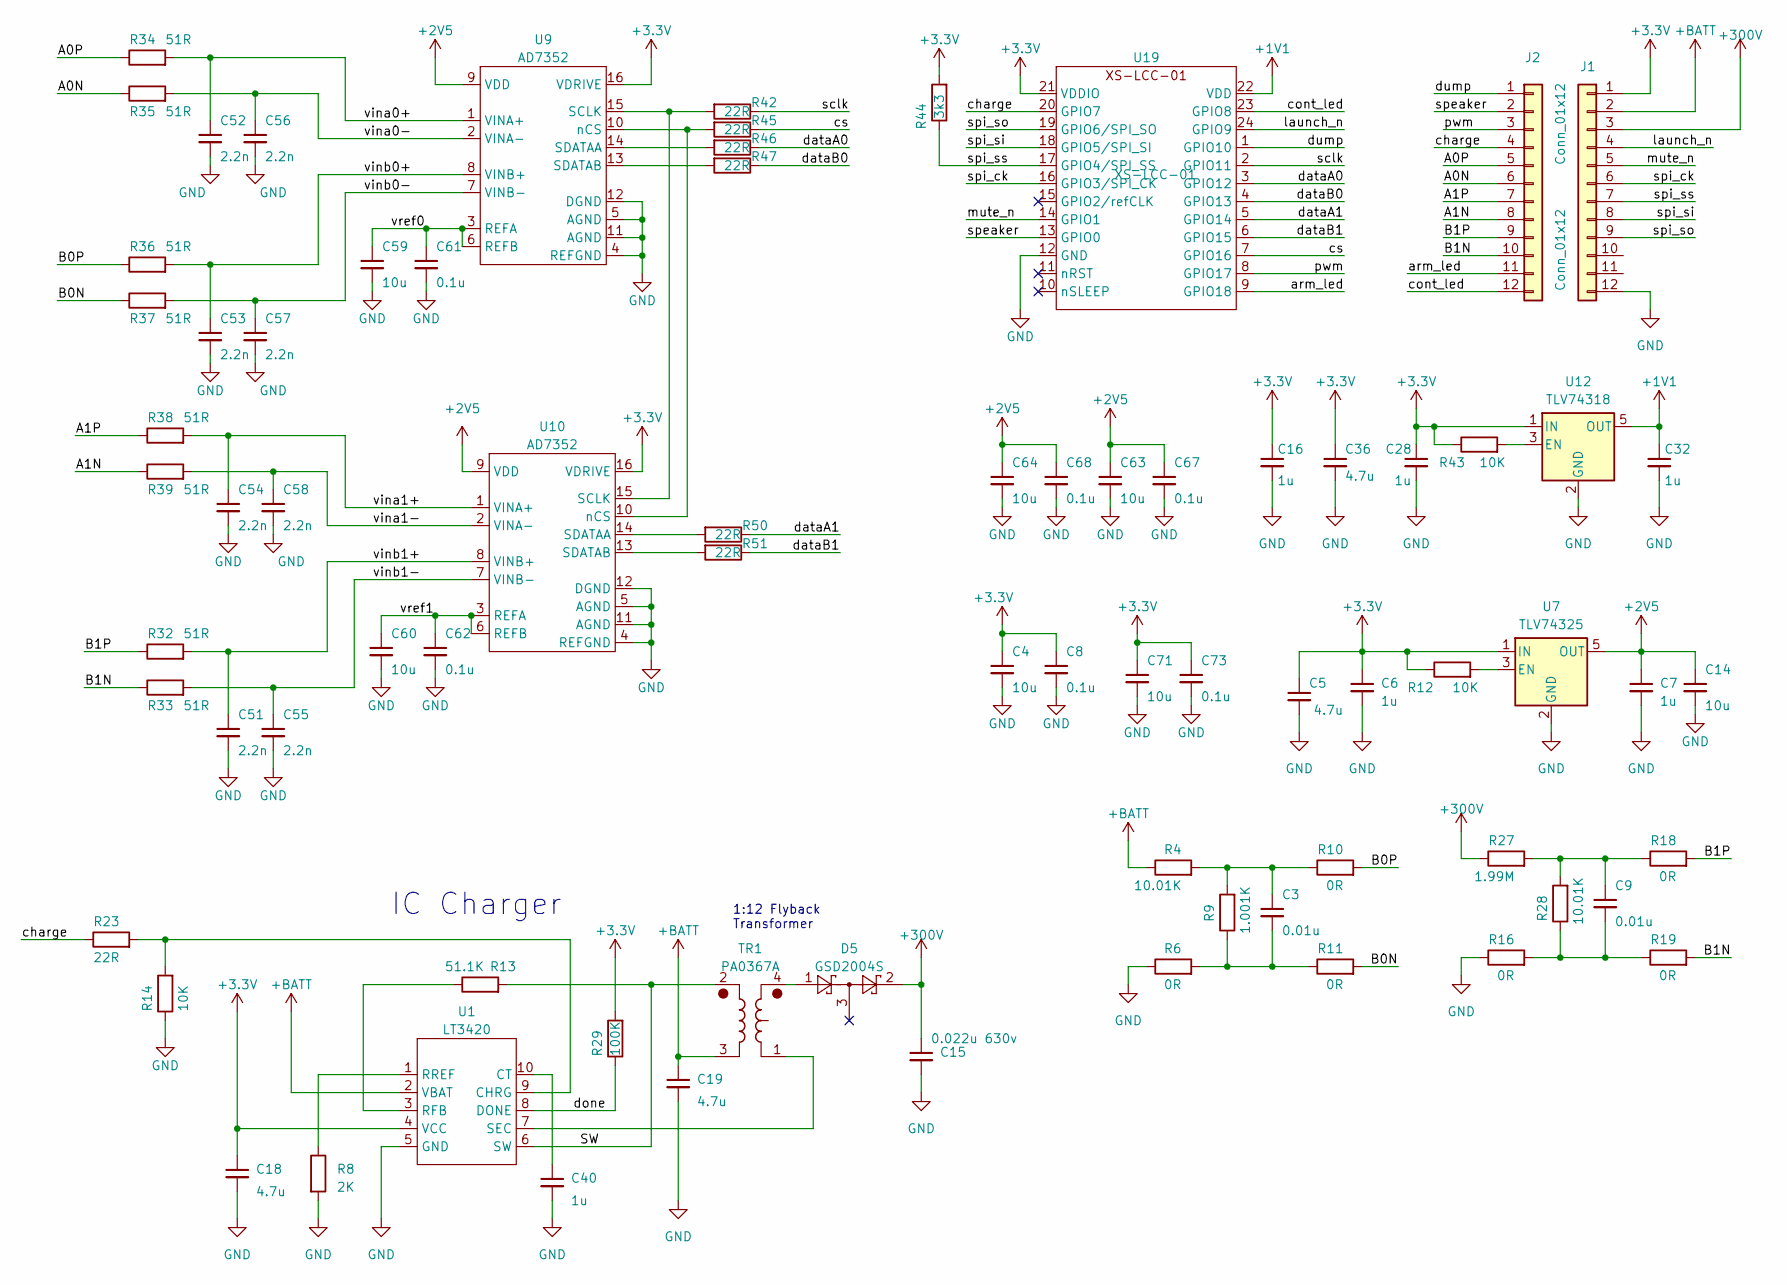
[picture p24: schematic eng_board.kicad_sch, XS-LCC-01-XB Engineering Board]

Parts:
C3, C9: 0.01u; C_0603_1608Metric
C4, C14, C59, C60, C63, C64, C71: 10u; C_1206_3216Metric
C5, C18, C19, C36: 4.7u; C_1206_3216Metric
C6, C7, C16, C28, C32, C40: 1u; C_0603_1608Metric
C8, C61, C62, C67, C68, C73: 0.1u; C_0603_1608Metric
C15: 0.022u 630v; C_1206_3216Metric
C51, C52, C53, C54, C55, C56, C57, C58: 2.2n; C_0603_1608Metric
D5: GSD2004S; SOT-23; JLC C85606
J1, J2: Conn_01x12; PinHeader_1x12_P2.54mm_Vertical
R4, R28: 10.01K; R_0603_1608Metric; JLC C778416
R6, R10, R11, R16, R18, R19: 0R; R_0603_1608Metric; JLC C778416
R8: 2K; R_0603_1608Metric; JLC C319700
R9: 1.001K; R_0603_1608Metric; JLC C778416
R12, R43: 10K; R_0603_1608Metric; JLC C778416
R13: 51.1K; R_0603_1608Metric; JLC C234563
R14: 10K; R_0603_1608Metric; JLC C491211
R23: 22R; R_0603_1608Metric; JLC C778416
R27: 1.99M; R_0603_1608Metric; JLC C778416
R29: 100K; R_0603_1608Metric; JLC C319967
R32, R33, R34, R35, R36, R37, R38, R39: 51R; R_0603_1608Metric; JLC C778416
R42, R45, R46, R47, R50, R51: 22R; R_0603_1608Metric; JLC C319967
R44: 3k3; R_0603_1608Metric; JLC C319967
TR1: PA0367A; PA0637A Pulse Coil 3D; JLC C5382098
U1: LT3420; MSOP-10_3x3mm_P0.5mm; JLC C670531
U7: TLV74325; SOT-23-5
U9, U10: AD7352; TSSOP-16_4.4x5mm_P0.65mm
U12: TLV74318; SOT-23-5
U19: XS-LCC-01; QFN-24-3x3mm

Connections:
+1V1: C32.1, U12.5 (OUT), U19.22 (VDD)
+2V5: C7.1, C14.1, C63.1, C64.1, C67.1, C68.1, U7.5 (OUT), U9.9 (VDD), U10.9 (VDD)
+3.3V: C4.1, C5.1, C6.1, C8.1, C16.1, C18.1, C28.1, C36.1, C71.1, C73.1, J1.1, R12.1, R29.2, R43.1, R44.2, U1.4 (VCC), U7.1 (IN), U9.16 (VDRIVE), U10.16 (VDRIVE), U12.1 (IN), U19.21 (VDDIO)
+300V: C15.1, D5.2 (NC), J1.3, R27.1
+BATT: C19.1, J1.2, R4.1, TR1.3, U1.2 (VBAT)
/A0N: J2.6, R35.1
/A0P: J2.5, R34.1
/A1N: J2.8, R39.1
/A1P: J2.7, R38.1
/B0N: R11.2, R37.1
/B0P: R10.2, R36.1
/B1N: J2.10, R19.2, R33.1
/B1P: J2.9, R18.2, R32.1
/SW: R13.2, TR1.2, U1.6 (SW)
/arm_led: J2.11, U19.9 (GPIO18)
/charge: J2.4, R23.1, U19.20 (GPIO7)
/cont_led: J2.12, U19.23 (GPIO8)
/cs: R45.1, U19.7 (GPIO16)
/dataA0: R46.1, U19.3 (GPIO12)
/dataA1: R50.1, U19.5 (GPIO14)
/dataB0: R47.1, U19.4 (GPIO13)
/dataB1: R51.1, U19.6 (GPIO15)
/done: R29.1, U1.8 (DONE)
/dump: J2.1, U19.1 (GPIO10)
/launch_n: J1.4, U19.24 (GPIO9)
/mute_n: J1.5, U19.14 (GPIO1)
/pwm: J2.3, U19.8 (GPIO17)
/sclk: R42.1, U19.2 (GPIO11)
/speaker: J2.2, U19.13 (GPIO0)
/spi_ck: J1.6, U19.16 (GPIO3/SPI_CK)
/spi_si: J1.8, U19.18 (GPIO5/SPI_SI)
/spi_so: J1.9, U19.19 (GPIO6/SPI_SO)
/spi_ss: J1.7, R44.1, U19.17 (GPIO4/SPI_SS)
/vina0+: C52.1, R34.2, U9.1 (VINA+)
/vina0-: C56.1, R35.2, U9.2 (VINA-)
/vina1+: C54.1, R38.2, U10.1 (VINA+)
/vina1-: C58.1, R39.2, U10.2 (VINA-)
/vinb0+: C53.1, R36.2, U9.8 (VINB+)
/vinb0-: C57.1, R37.2, U9.7 (VINB-)
/vinb1+: C51.1, R32.2, U10.8 (VINB+)
/vinb1-: C55.1, R33.2, U10.7 (VINB-)
/vref0: C59.1, C61.1, U9.3 (REFA), U9.6 (REFB)
/vref1: C60.1, C62.1, U10.3 (REFA), U10.6 (REFB)
GND: C4.2, C5.2, C6.2, C7.2, C8.2, C14.2, C15.2, C16.2, C18.2, C19.2, C28.2, C32.2, C36.2, C40.2, C51.2, C52.2, C53.2, C54.2, C55.2, C56.2, C57.2, C58.2, C59.2, C60.2, C61.2, C62.2, C63.2, C64.2, C67.2, C68.2, C71.2, C73.2, J1.12, R6.1, R8.2, R14.1, R16.1, U1.5 (GND), U7.2 (GND), U9.4 (REFGND), U9.5 (AGND), U9.11 (AGND), U9.12 (DGND), U10.4 (REFGND), U10.5 (AGND), U10.11 (AGND), U10.12 (DGND), U12.2 (GND), U19.12 (GND)
unnamed: C3.1, R4.2, R9.2, R10.1
unnamed: C3.2, R6.2, R9.1, R11.1
unnamed: C9.1, R18.1, R27.2, R28.2
unnamed: C9.2, R16.2, R19.1, R28.1
unnamed: D5.1, TR1.4
unnamed: R14.2, R23.2, U1.9 (CHRG)
unnamed: C40.1, U1.10 (CT)
unnamed: R13.1, U1.3 (RFB)
unnamed: R8.1, U1.1 (RREF)
unnamed: TR1.1, U1.7 (SEC)
unnamed: R12.2, U7.3 (EN)
unnamed: R46.2, U9.14 (SDATAA)
unnamed: R47.2, U9.13 (SDATAB)
unnamed: R42.2, U9.15 (SCLK), U10.15 (SCLK)
unnamed: R50.2, U10.14 (SDATAA)
unnamed: R51.2, U10.13 (SDATAB)
unnamed: R45.2, U9.10 (nCS), U10.10 (nCS)
unnamed: R43.2, U12.3 (EN)

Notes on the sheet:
IC Charger
1:12 Flyback Transformer

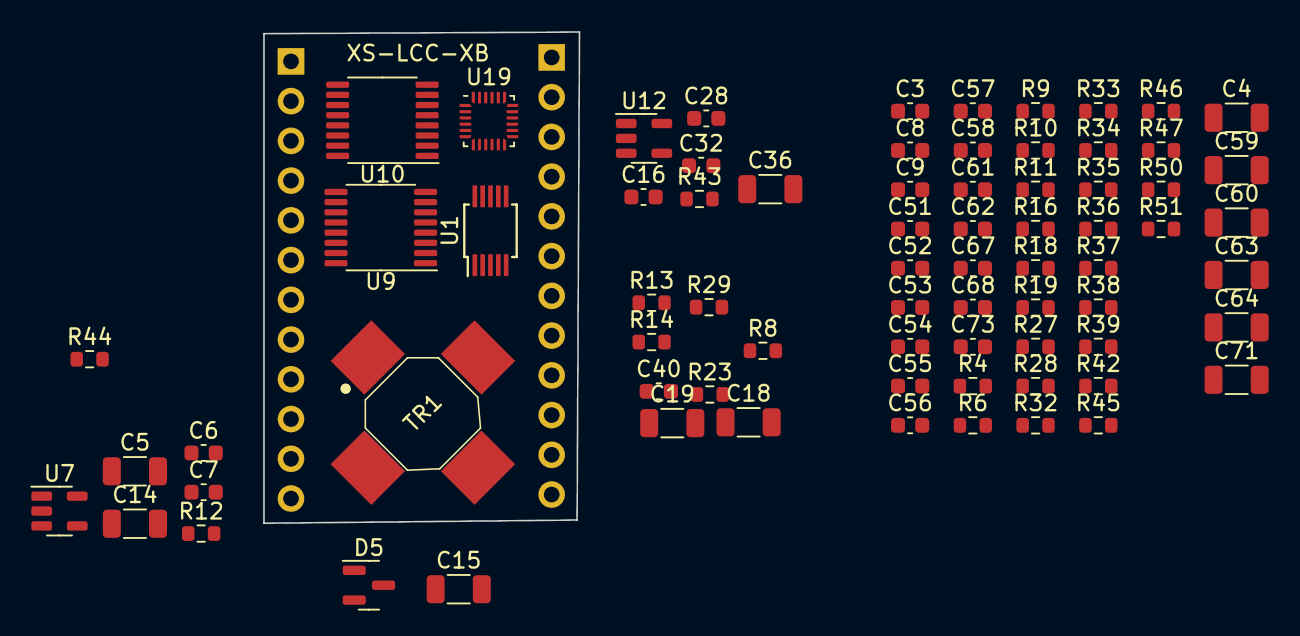
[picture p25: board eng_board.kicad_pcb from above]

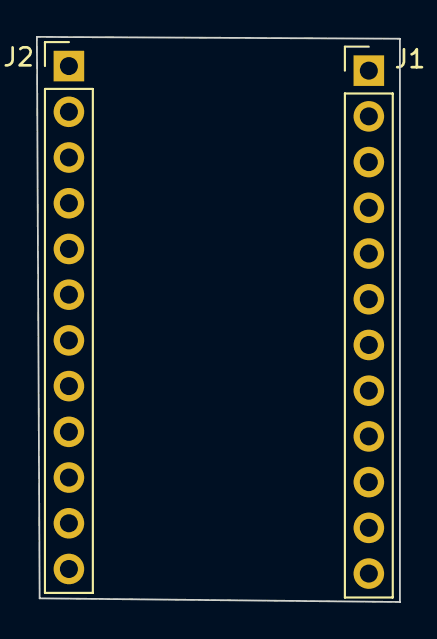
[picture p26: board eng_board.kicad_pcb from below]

Board: 6 copper layers, 20.2 x 31.4 mm, 76 parts (2 on the bottom side), 62 nets.

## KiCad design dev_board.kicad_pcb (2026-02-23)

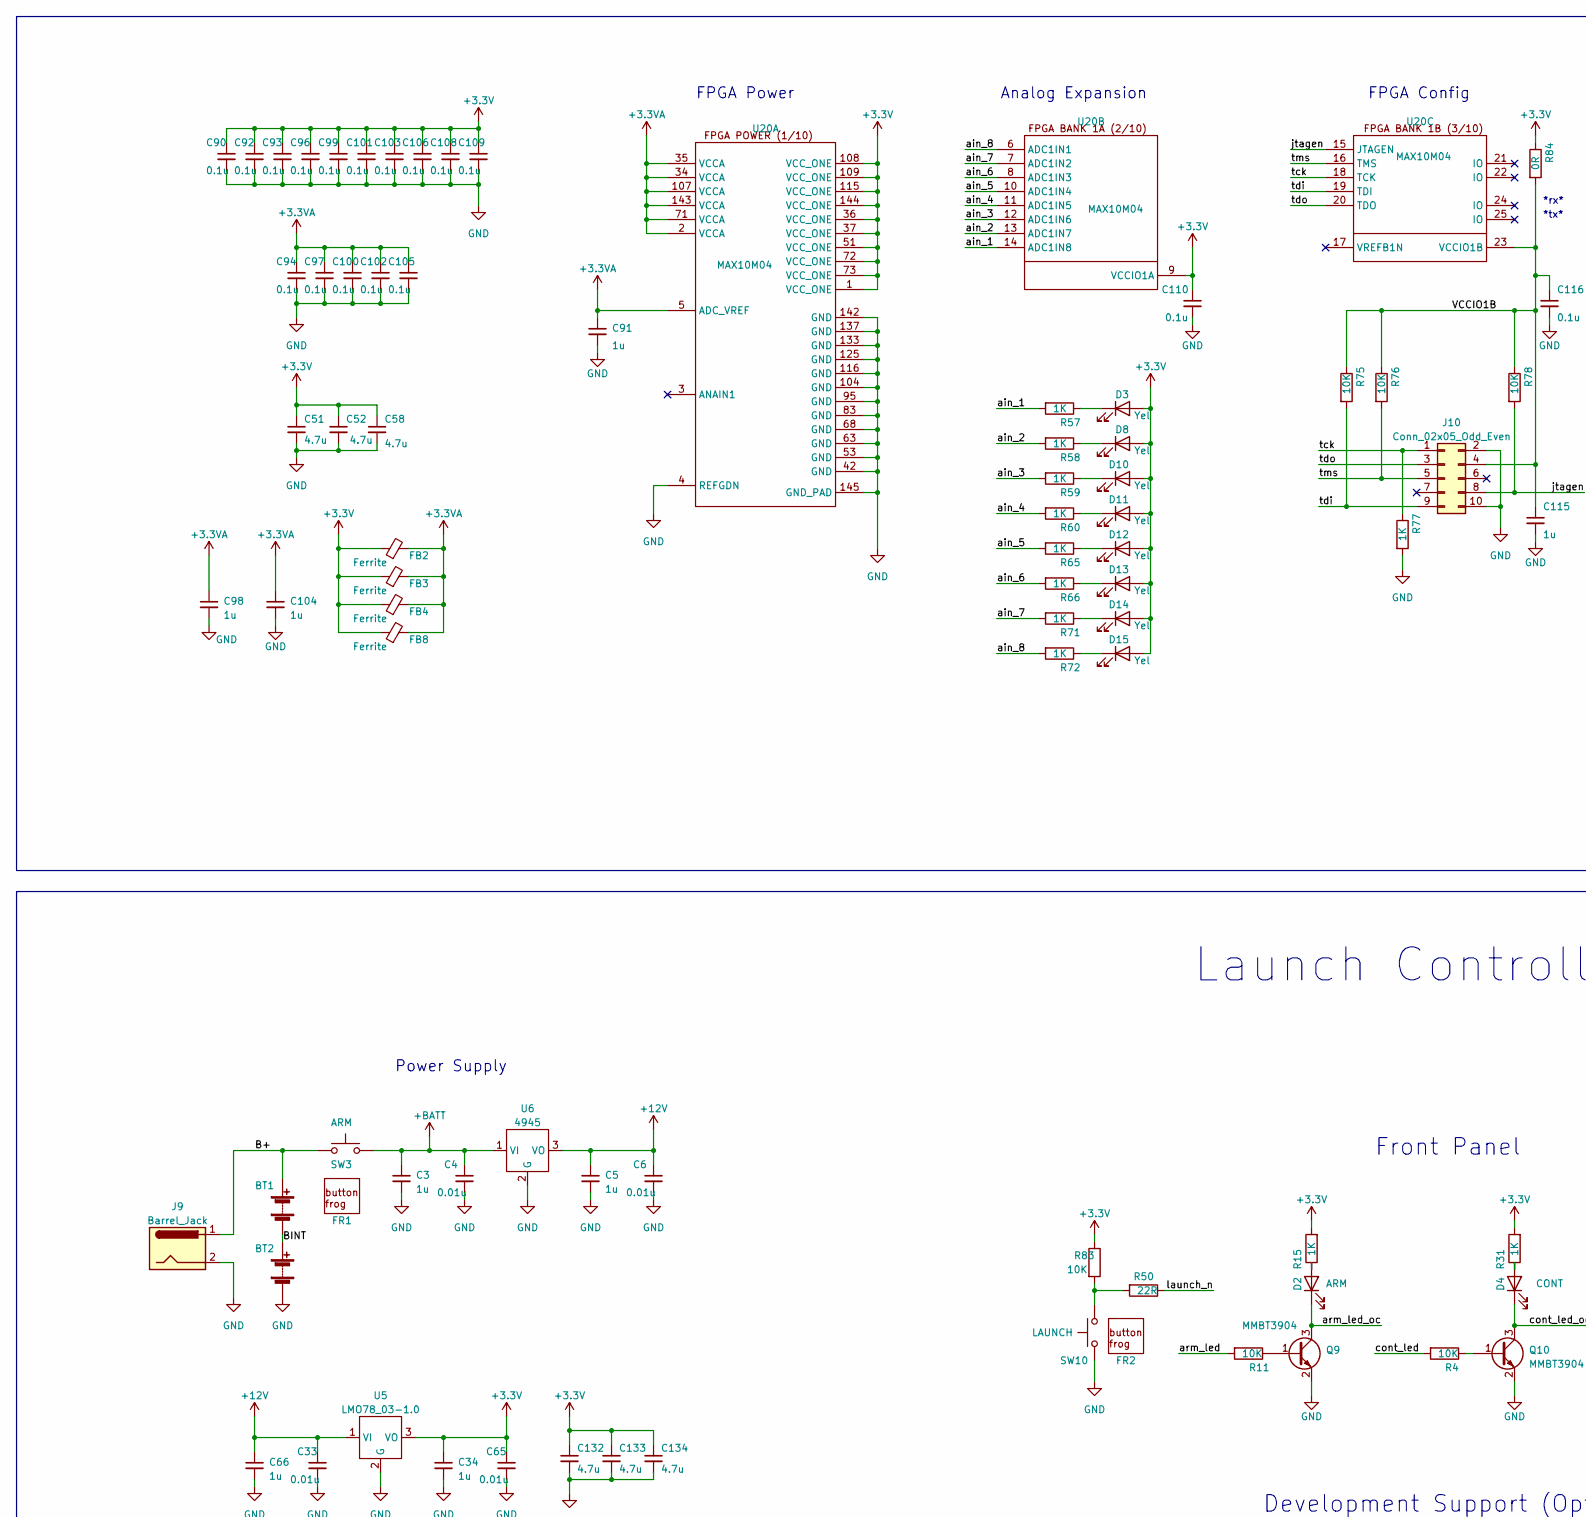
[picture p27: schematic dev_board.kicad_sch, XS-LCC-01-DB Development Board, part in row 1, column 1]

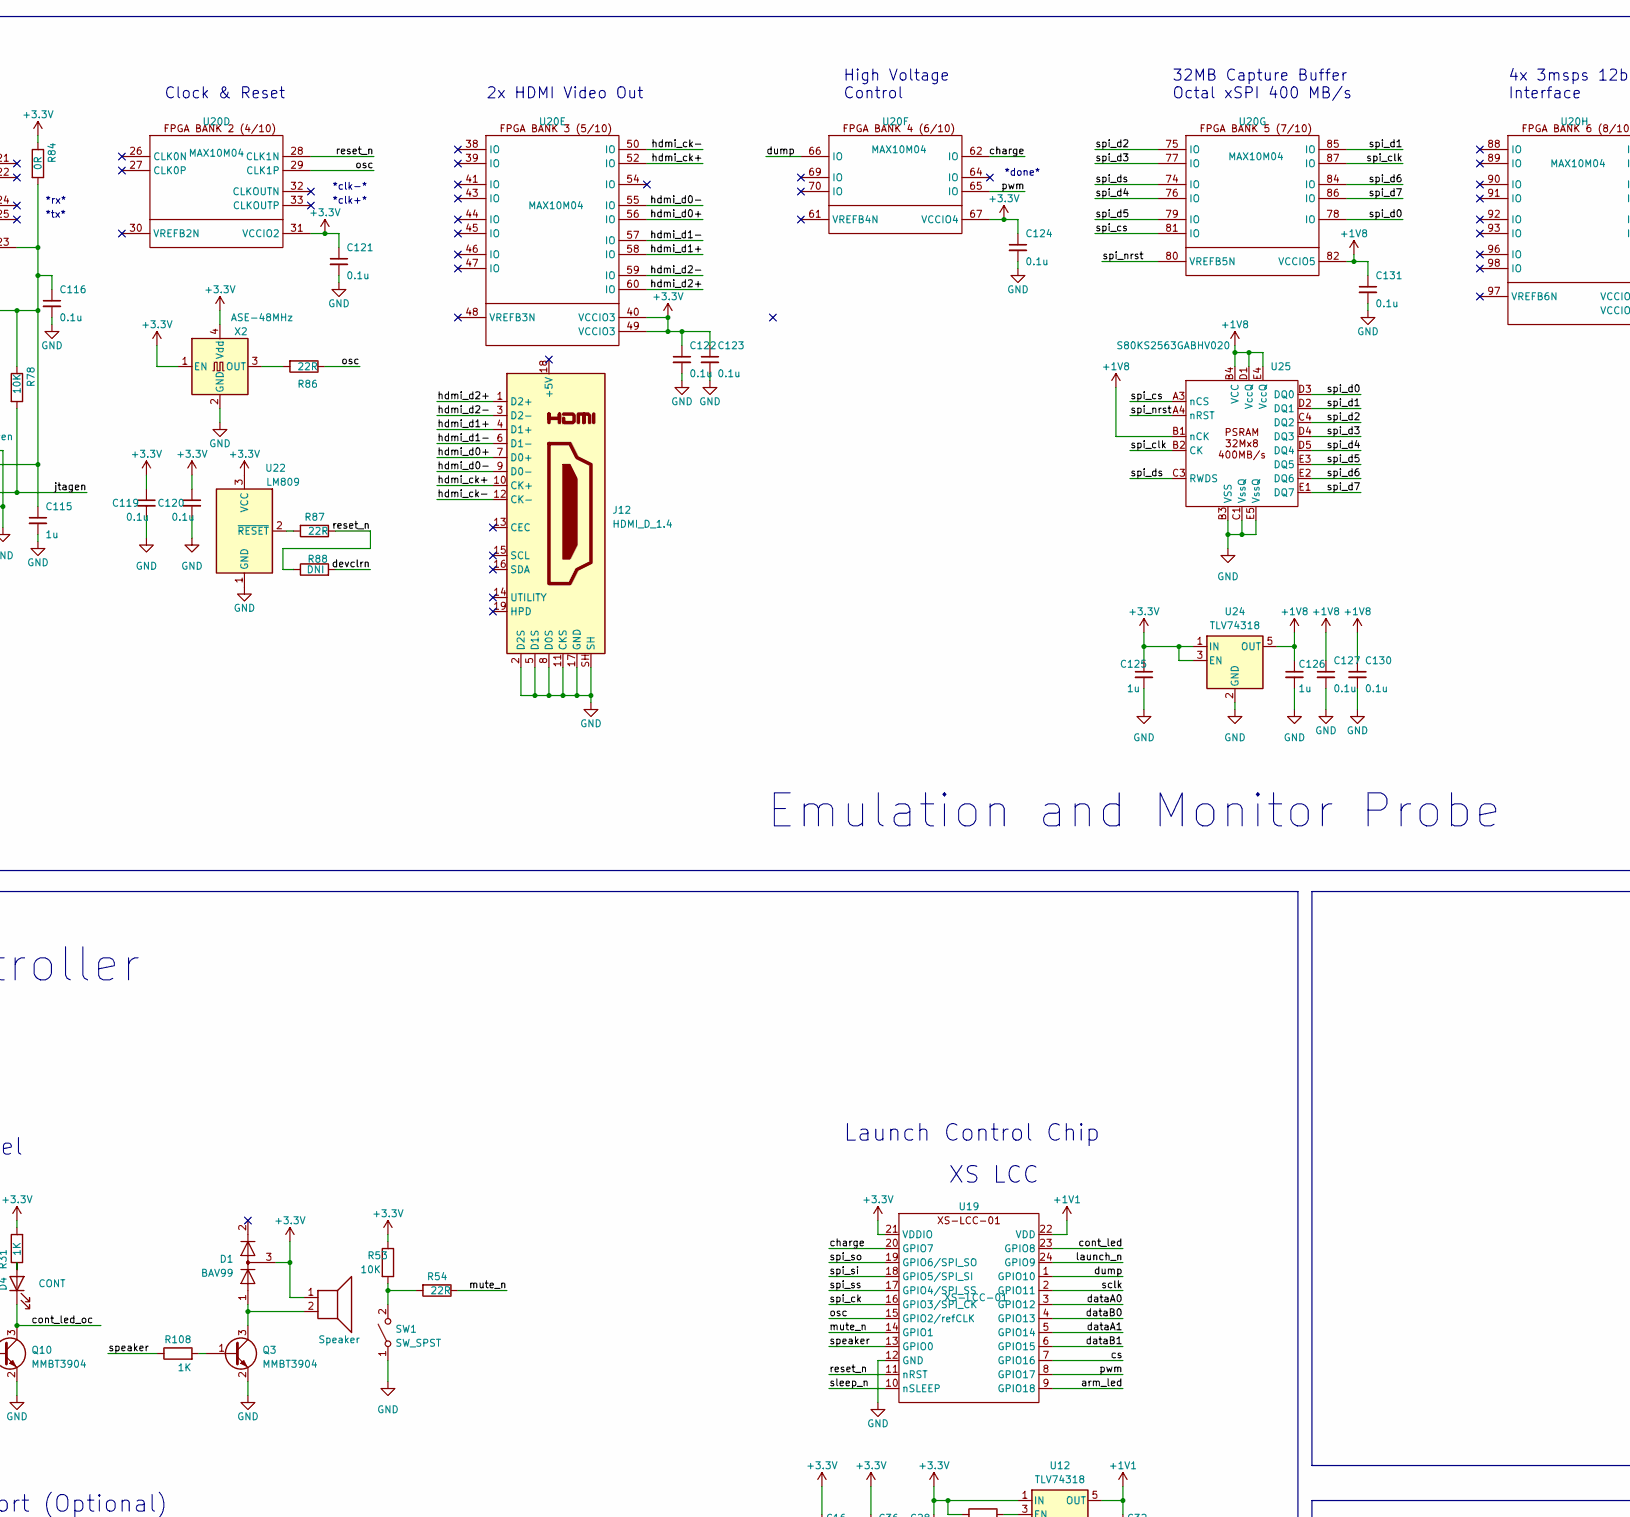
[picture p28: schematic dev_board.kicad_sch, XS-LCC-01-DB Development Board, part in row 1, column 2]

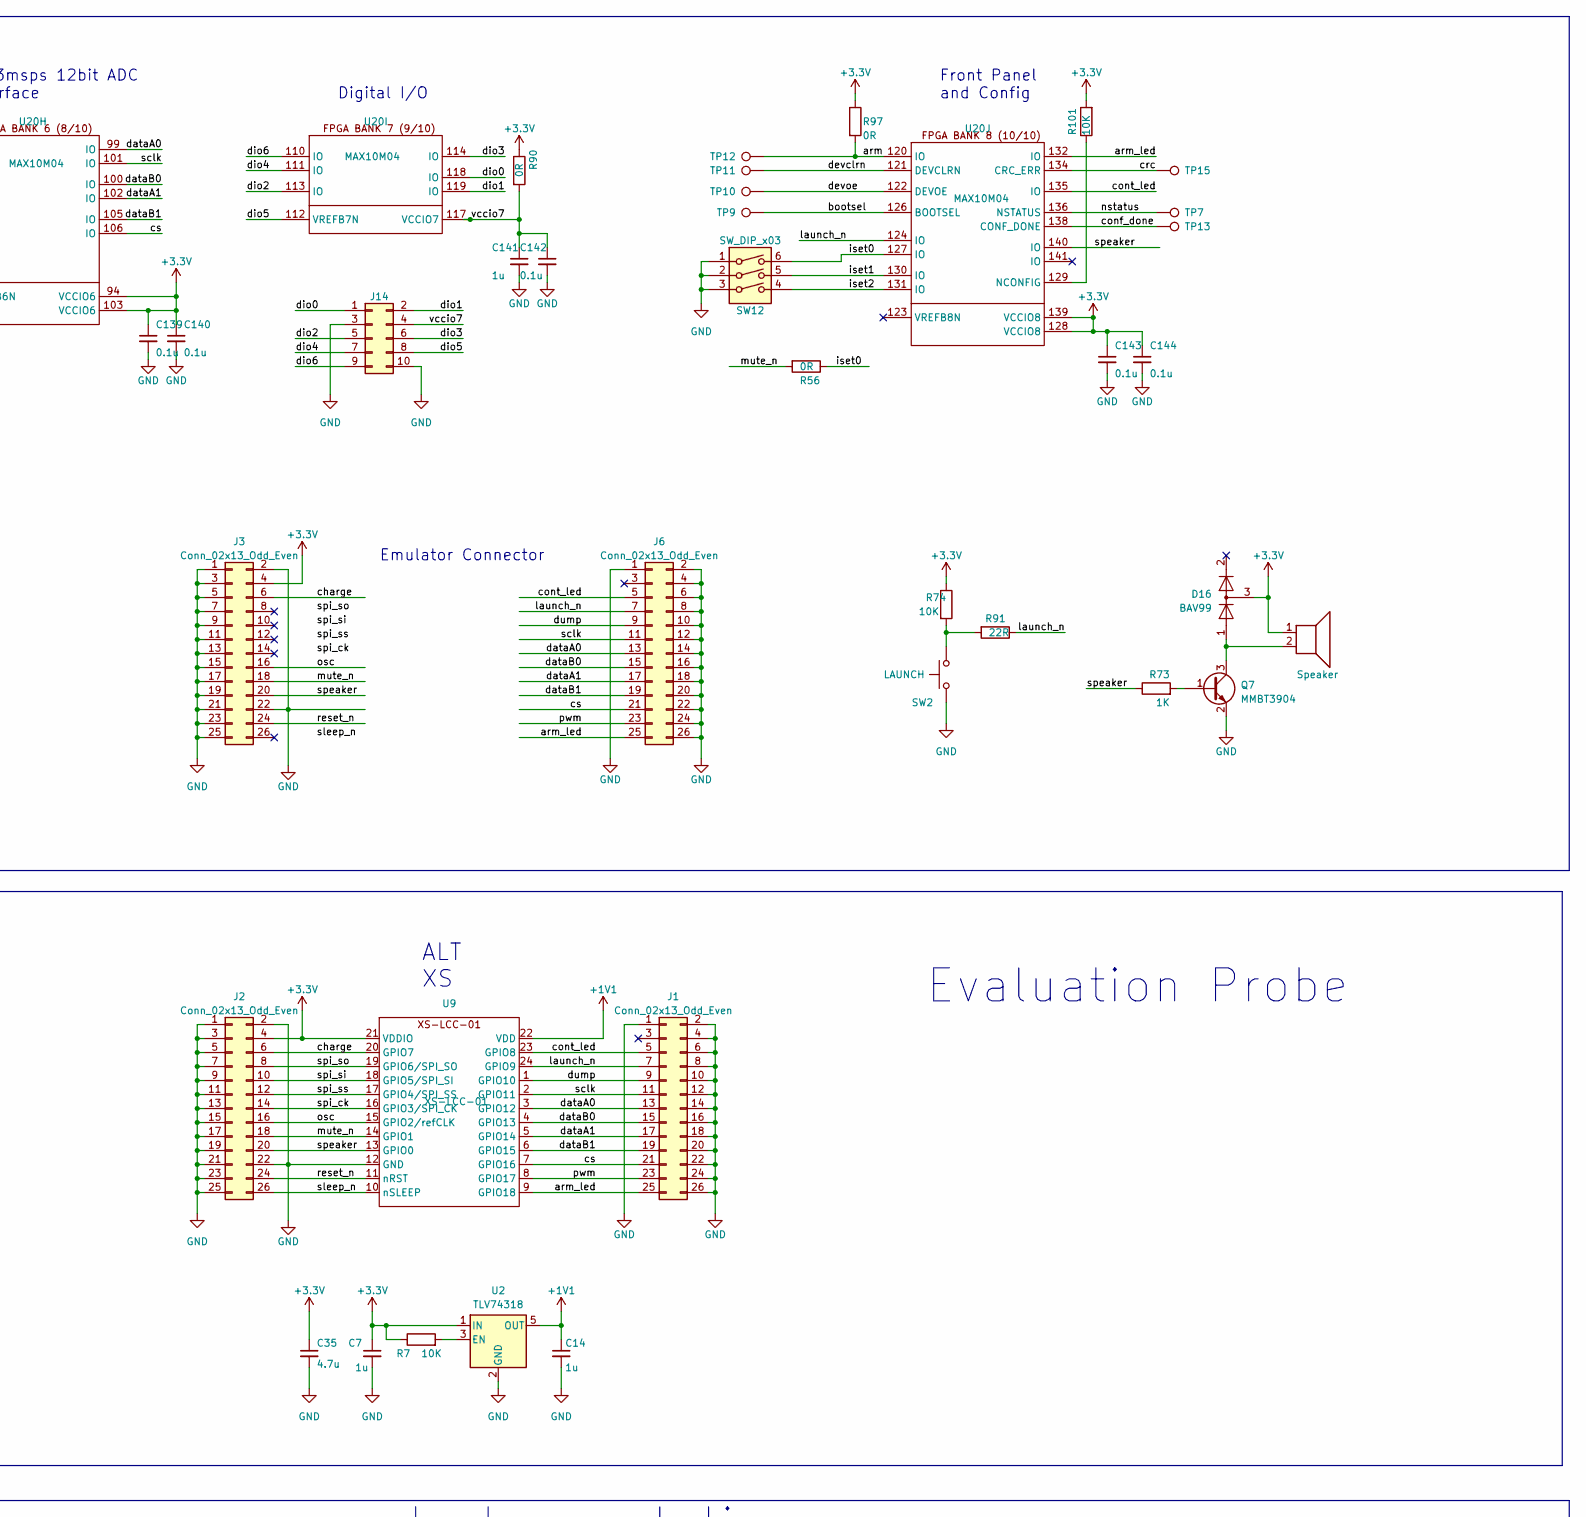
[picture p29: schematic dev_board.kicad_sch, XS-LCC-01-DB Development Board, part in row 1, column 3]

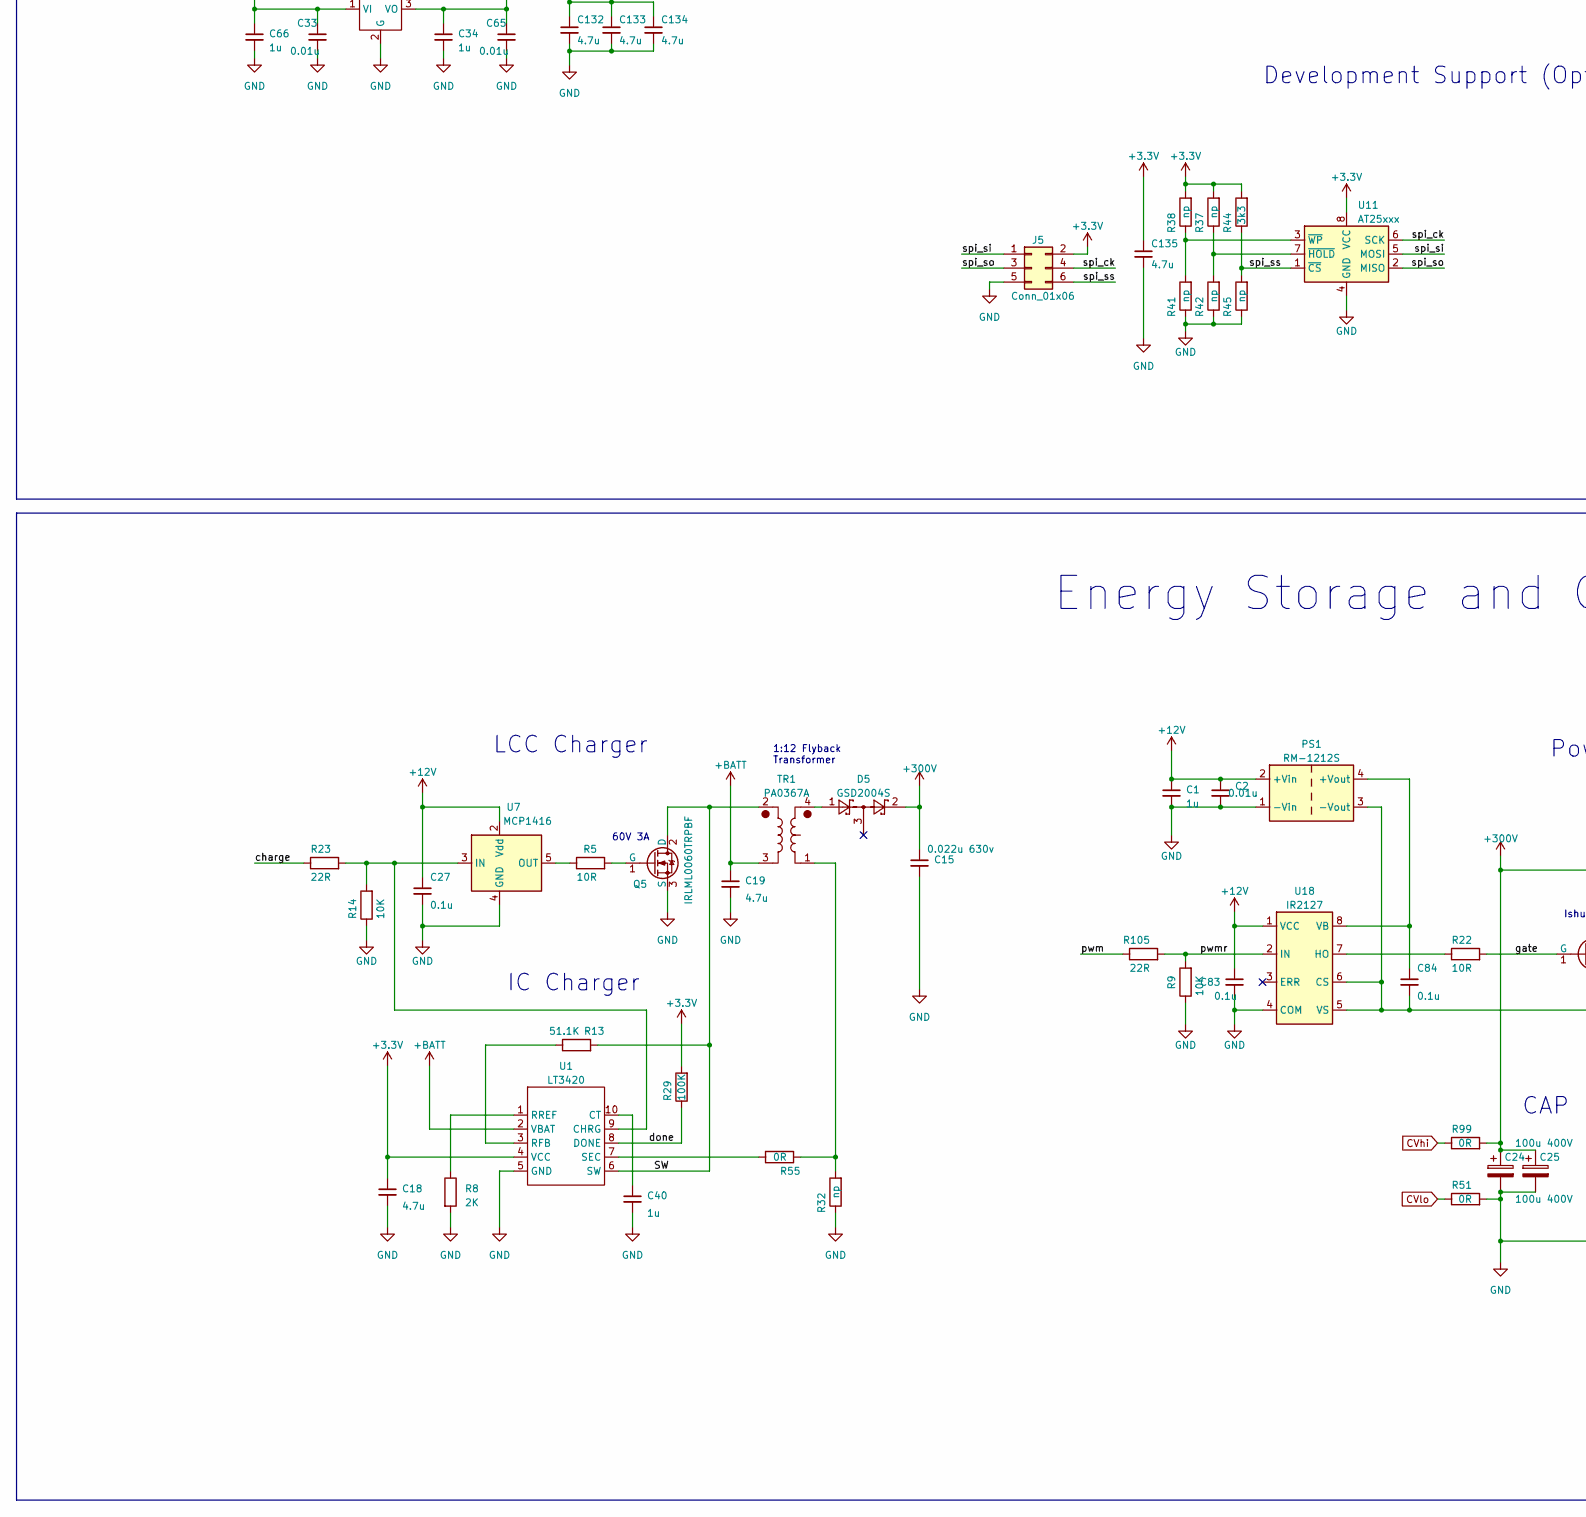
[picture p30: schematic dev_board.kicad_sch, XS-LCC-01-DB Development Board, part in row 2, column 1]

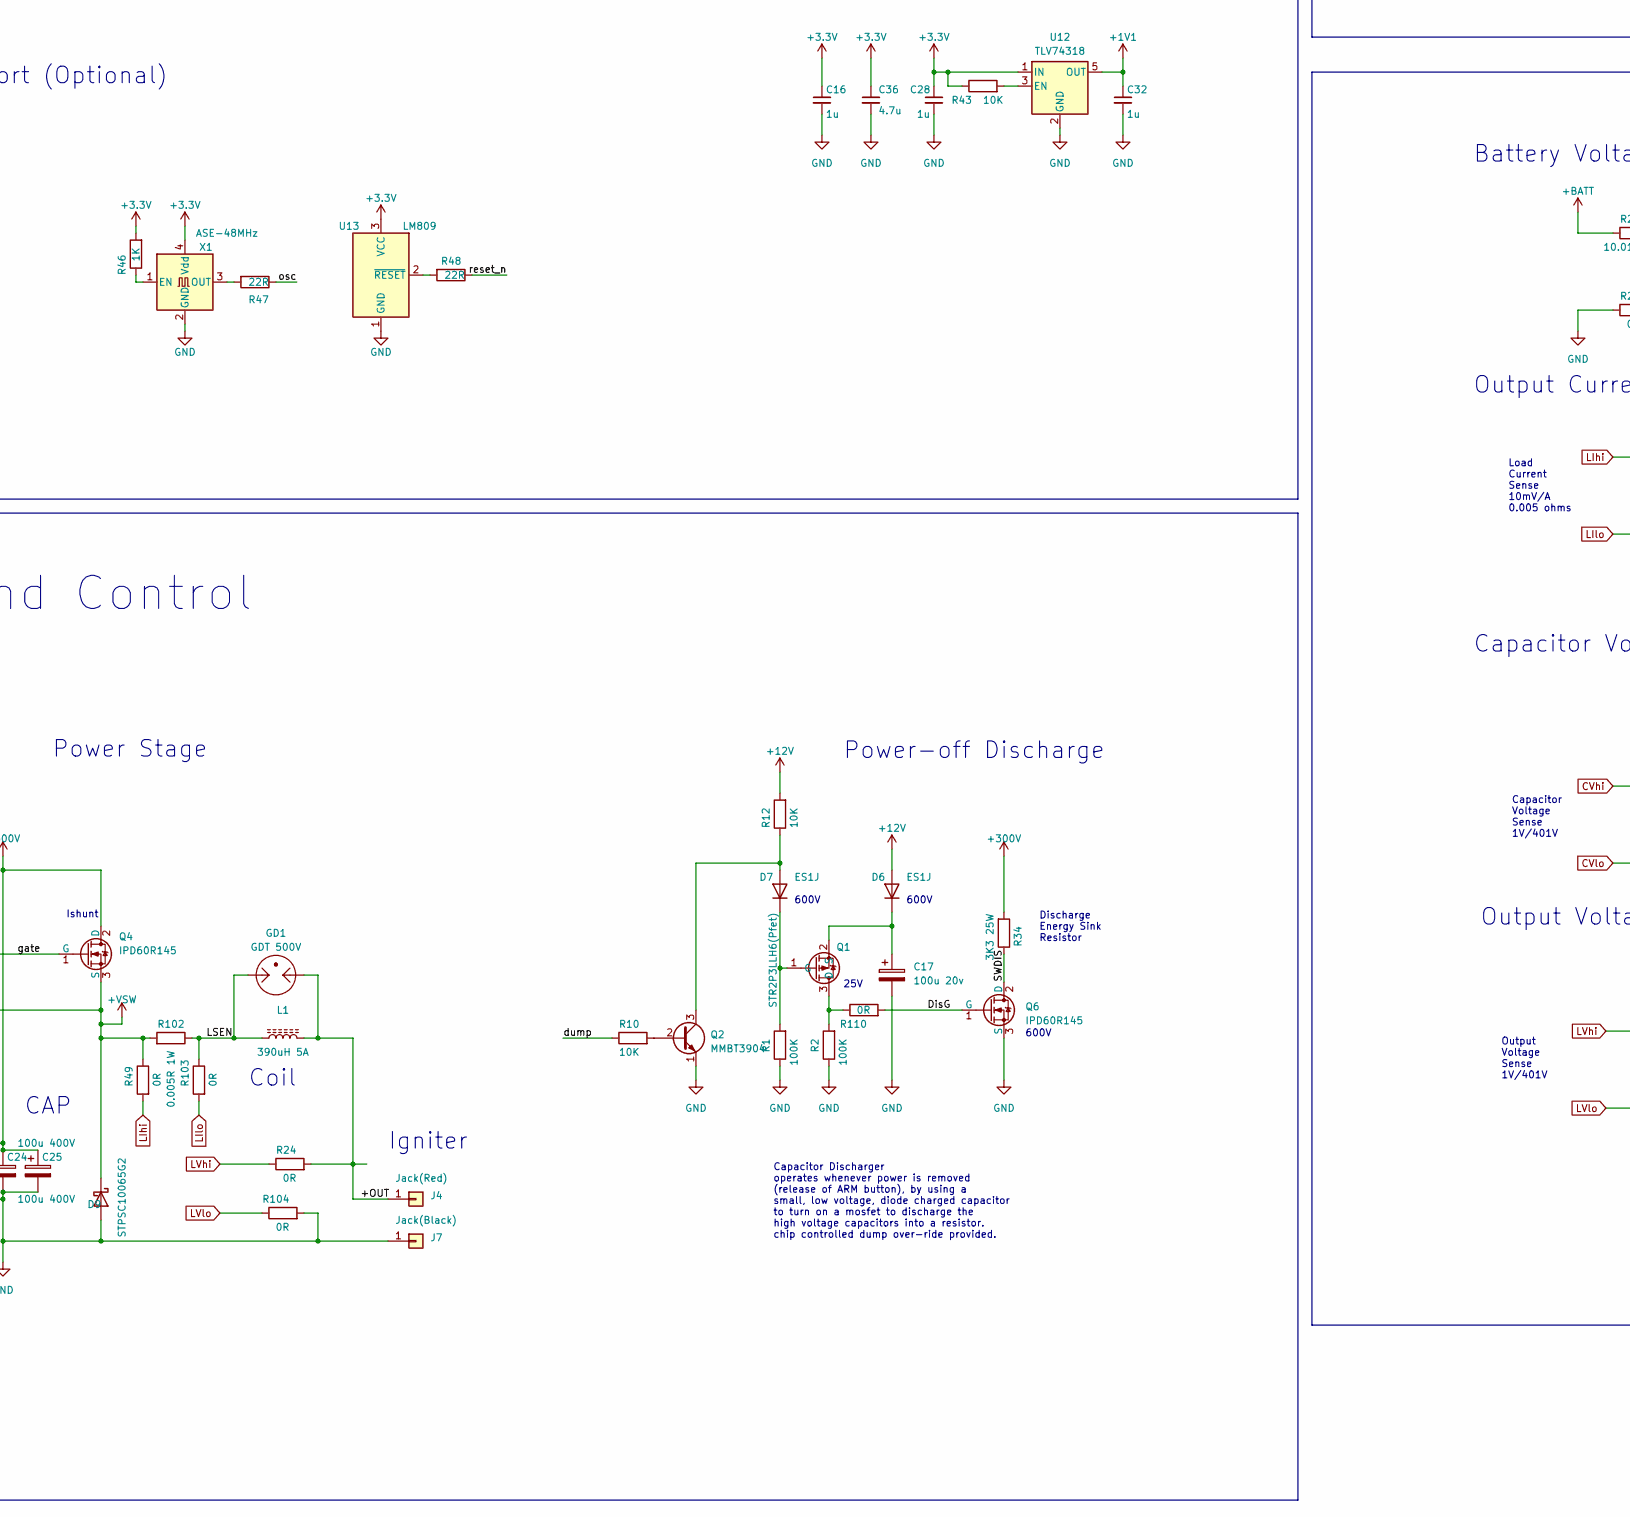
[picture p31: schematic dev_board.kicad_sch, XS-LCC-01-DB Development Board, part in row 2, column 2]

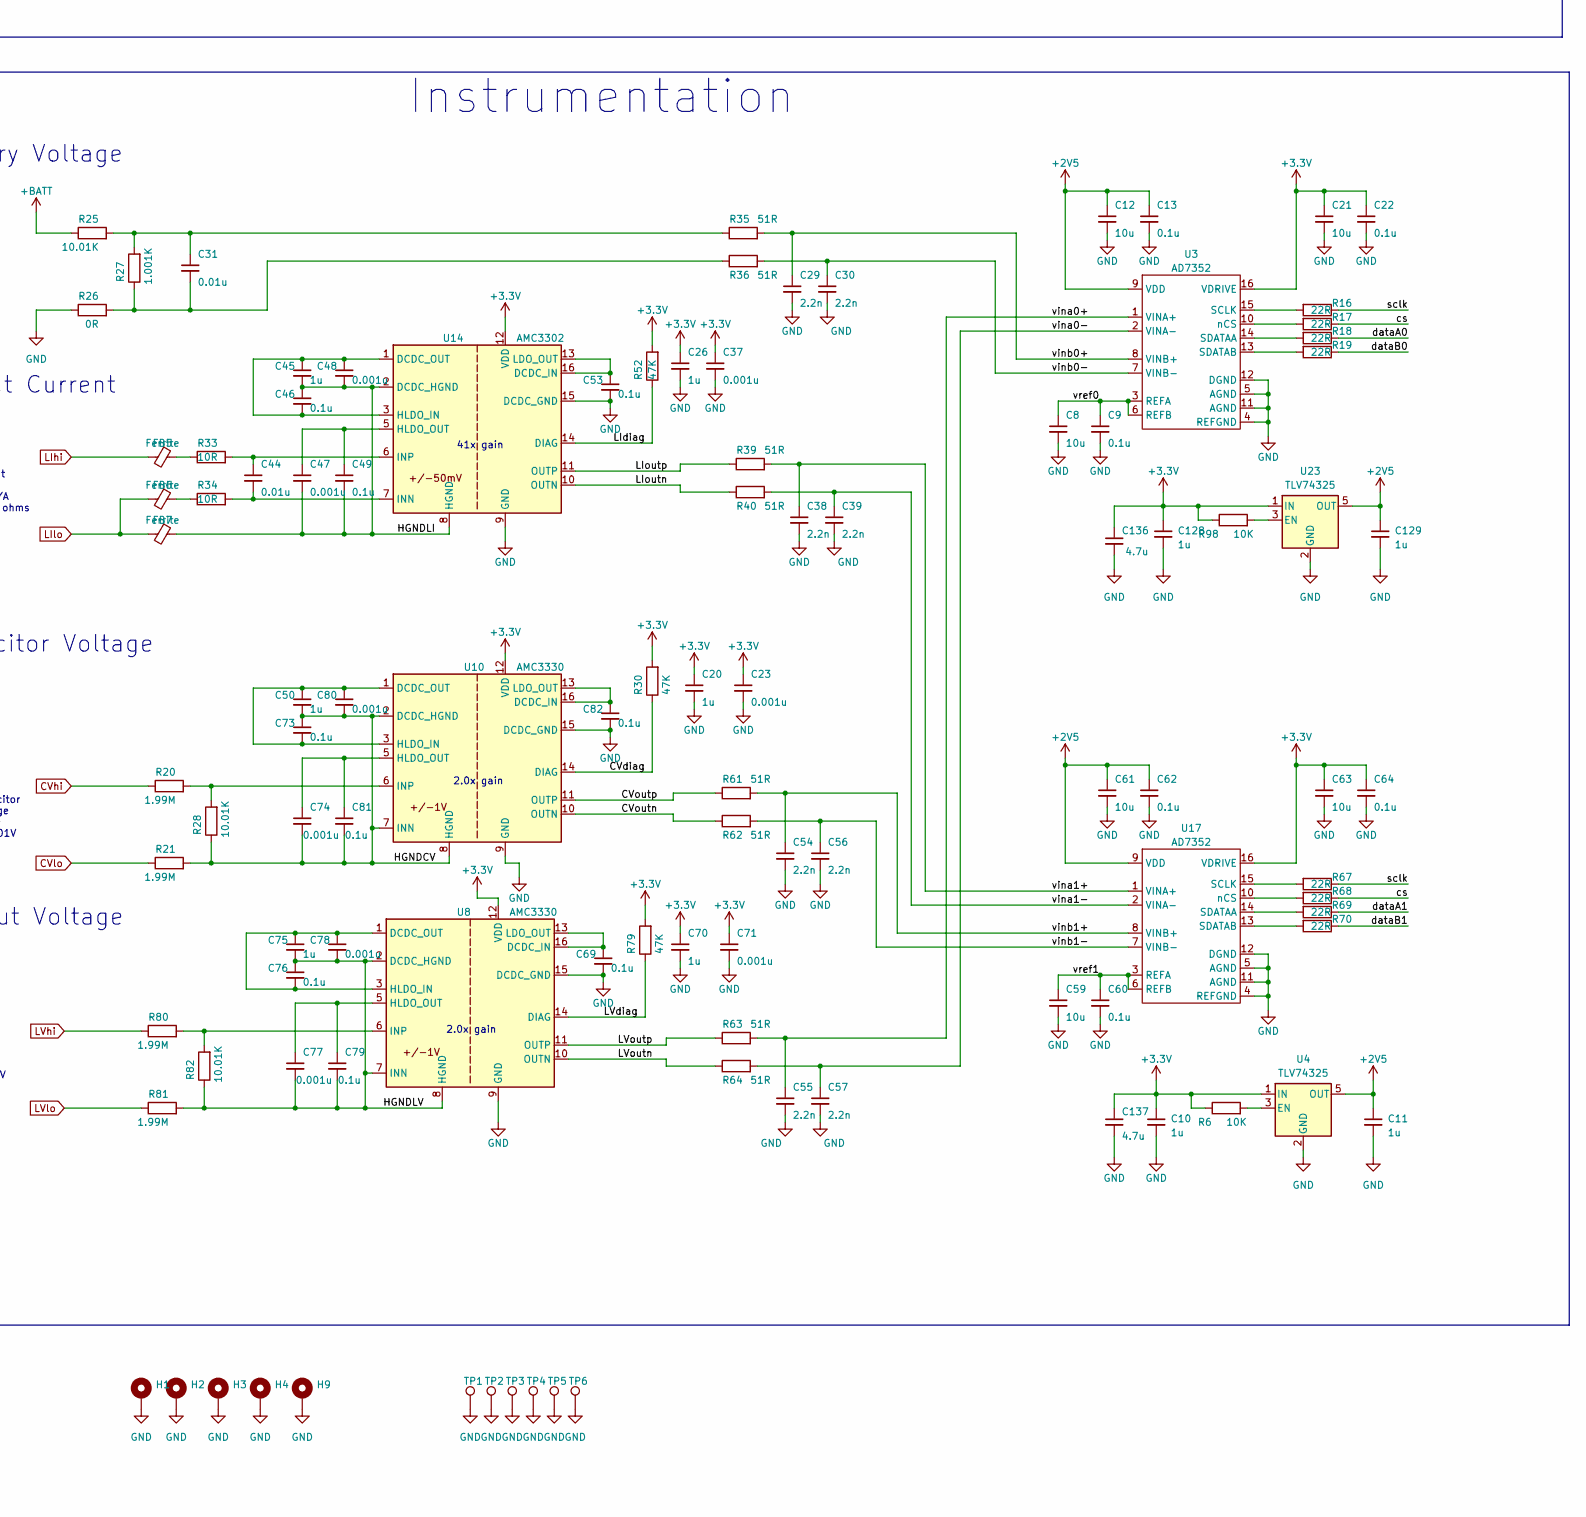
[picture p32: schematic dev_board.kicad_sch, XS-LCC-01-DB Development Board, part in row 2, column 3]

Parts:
BT1, BT2: BatteryHolder_Keystone_2462_2xAA
C1, C3, C5, C7, C10, C11, C14, C16, C20, C26, C28, C32, C34, C40, C45, C50, C66, C70, C75, C91, C98, C104, C115, C125, C126, C128, C129, C141: 1u; C_0603_1608Metric
C2, C4, C6, C31, C33, C44, C65: 0.01u; C_0603_1608Metric
C8, C12, C21, C59, C61, C63: 10u; C_1206_3216Metric
C9, C13, C22, C27, C46, C49, C53, C60, C62, C64, C69, C73, C76, C79, C81, C82, C83, C84, C90, C92, C93, C94, C96, C97, C99, C100, C101, C102, C103, C105, C106, C108, C109, C110, C116, C119, C120, C121, C122, C123, C124, C127, C130, C131, C139, C140, C142, C143, C144: 0.1u; C_0603_1608Metric
C15: 0.022u 630v; C_1206_3216Metric
C17: 100u 20v; C_Radial_D5.0mm_H7.0mm_P2.00mm
C18, C19, C35, C36, C51, C52, C58, C132, C133, C134, C135, C136, C137: 4.7u; C_1206_3216Metric
C23, C37, C47, C48, C71, C74, C77, C78, C80: 0.001u; C_0603_1608Metric
C24, C25: 100u 400V; CP_Radial_D16.0mm_P7.50mm
C29, C30, C38, C39, C54, C55, C56, C57: 2.2n; C_0603_1608Metric
D1, D16: BAV99; SOT-23
D2: ARM; LED_0603_1608Metric
D3, D8, D10, D11, D12, D13, D14, D15: Yel; LED_0603_1608Metric
D4: CONT; LED_0603_1608Metric
D5: GSD2004S; SOT-23; JLC C85606
D6, D7: ES1J; D_SMA; JLC C99410
D9: ‎STPSC10065G2; TO-263-2_TabPin1; JLC C602663
FB2, FB3, FB4, FB5, FB6, FB7, FB8: Ferrite; L_0603_1608Metric
FR1, FR2: button_frog
GD1: GDT 500V; C_1812_4532Metric_Pad1.57x3.40mm_HandSolder
H1, H2, H3, H4, H9: MountingHole_3mm_Pad
J1, J2, J3, J6: Conn_02x13_Odd_Even; PinSocket_2x13_P2.54mm_Vertical
J4: Jack(Red); CalTest_CT3151
J5: Conn_01x06; PinHeader_2x03_P2.54mm_Vertical
J7: Jack(Black); CalTest_CT3151
J9: Barrel_Jack; BarrelJack_CUI_PJ-063AH_Horizontal
J10, J14: Conn_02x05_Odd_Even; PinHeader_2x05_P2.54mm_Vertical
J12: HDMI_D_1.4; HDMI_A_Amphenol_10029449-x01xLF_Horizontal
L1: 390uH 5A; L_Toroid_Vertical_L35.6mm_W17.8mm_P12.70mm_Pulse_E
LS1, LS2: Speaker; PUIAudio_SMT_0825_S_4_R
PS1: RM-1212S; Converter_DCDC_Murata_MEE1SxxxxSC_THT
Q1: STR2P3LLH6(Pfet); SOT-23
Q2, Q3, Q7, Q9, Q10: MMBT3904; SOT-23
Q4, Q6: IPD60R145; TO-252-2; JLC C3277918
Q5: IRLML0060TRPBF; SOT-23; JLC C3277918
R1, R2, R29: 100K; R_0603_1608Metric; JLC C319967
R4, R11, R75, R76, R78, R101: 10K; R_0603_1608Metric; JLC C319967
R5, R22, R33, R34: 10R; R_0603_1608Metric; JLC C778416
R6, R7, R43, R98: 10K; R_0603_1608Metric; JLC C778416
R8: 2K; R_0603_1608Metric; JLC C319700
R9, R12, R14, R53, R74, R83: 10K; R_0603_1608Metric; JLC C491211
R10: 10K; R_0603_1608Metric
R13: 51.1K; R_0603_1608Metric; JLC C234563
R15, R31, R46, R57, R58, R59, R60, R65, R66, R71, R72, R73, R77, R108: 1K; R_0603_1608Metric; JLC C319967
R16, R17, R18, R19, R47, R48, R50, R54, R67, R68, R69, R70, R86, R87, R91: 22R; R_0603_1608Metric; JLC C319967
R20, R21, R80, R81: 1.99M; R_0603_1608Metric; JLC C778416
R23, R105: 22R; R_0603_1608Metric; JLC C778416
R24, R26, R49, R51, R56, R99, R103, R104: 0R; R_0603_1608Metric; JLC C778416
R25, R28, R82: 10.01K; R_0603_1608Metric; JLC C778416
R27: 1.001K; R_0603_1608Metric; JLC C778416
R30, R52, R79: 47K; R_0603_1608Metric; JLC C778416
R32, R37, R38, R41, R42, R45: np; R_0603_1608Metric
R35, R36, R39, R40, R61, R62, R63, R64: 51R; R_0603_1608Metric; JLC C778416
R44: 3k3; R_0603_1608Metric; JLC C319967
R55, R84, R90, R110: 0R; R_0603_1608Metric; JLC C319967
R88: DNI; R_0603_1608Metric; JLC C491211
R97: 0R; R_0603_1608Metric; JLC C491211
R102: 0.005R 1W; R_2818 current sense
SW1: SW_SPST; SW_E-Switch_EG1224_SPDT_Angled
SW2, SW10: LAUNCH; SW_SPST_HP03
SW3: ARM; SW_SPST_HP03
SW12: SW_DIP_x03; SW_DIP_SPSTx03_Slide_Omron_A6S-310x_W8.9mm_P2.54mm
TP1, TP2, TP3, TP4, TP5, TP6: TestPoint_Keystone_5000-5004_Miniature
TP7, TP13: TestPoint_Pad_D1.0mm
TP9, TP10, TP11, TP12, TP15: TestPoint_Pad_D1.5mm
TR1: PA0367A; PA0637A Pulse Coil 3D; JLC C5382098
U1: LT3420; MSOP-10_3x3mm_P0.5mm; JLC C670531
U2, U12, U24: TLV74318; SOT-23-5
U3, U17: AD7352; TSSOP-16_4.4x5mm_P0.65mm
U4, U23: TLV74325; SOT-23-5
U5: LMO78_03-1.0; Converter_DCDC_Murata_OKI-78SR_Horizontal
U6: 4945; Converter_DCDC_Murata_OKI-78SR_Horizontal
U7: MCP1416; SOT-23-5
U8, U10: AMC3330; SOIC-16W_7.5x10.3mm_P1.27mm
U9, U19: XS-LCC-01; QFN-24-3x3mm
U11: AT25xxx; SOIC-8_3.9x4.9mm_P1.27mm
U13, U22: LM809; SOT-23
U14: AMC3302; SOIC-16W_7.5x10.3mm_P1.27mm
U18: IR2127; SOIC-8_3.9x4.9mm_P1.27mm; JLC C356723
U20: MAX10M04; EQFP-144-1EP_20x20mm_P0.5mm_EP8.93x8.7mm_ThermalVias
U25: S80KS2563GABHV020; FBGA-24_6mmx8mm_Layout5x5_P1.00mm
X1, X2: ASE-48MHz; Oscillator_SMD_Abracon_ASV-4Pin_7.0x5.1mm_HandSoldering

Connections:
+1V1: C14.1, C32.1, U2.5 (OUT), U9.22 (VDD), U12.5 (OUT), U19.22 (VDD)
+1V8: C126.1, C127.1, C130.1, C131.1, U20.82 (VCCIO5), U24.5 (OUT), U25.B1 (nCK), U25.B4 (VCC), U25.D1 (VccQ), U25.E4 (VccQ)
+2V5: C11.1, C12.1, C13.1, C61.1, C62.1, C129.1, U3.9 (VDD), U4.5 (OUT), U17.9 (VDD), U23.5 (OUT)
+3.3V: C7.1, C10.1, C16.1, C18.1, C20.1, C21.1, C22.1, C23.1, C26.1, C28.1, C34.1, C35.1, C36.1, C37.1, C51.1, C52.1, C58.1, C63.1, C64.1, C65.1, C70.1, C71.1, C90.1, C92.1, C93.1, C96.1, C99.1, C101.1, C103.1, C106.1, C108.1, C109.1, C110.1, C119.1, C120.1, C121.1, C122.1, C123.1, C124.1, C125.1, C128.1, C132.1, C133.1, C134.1, C135.1, C136.1, C137.1, C139.1, C140.1, C143.1, C144.1, D1.3 (K), D3.2 (A), D8.2 (A), D10.2 (A), D11.2 (A), D12.2 (A), D13.2 (A), D14.2 (A), D15.2 (A), D16.3 (K), FB2.1, FB3.1, FB4.1, FB8.1, J2.4, J3.4, J5.2, LS1.1, LS2.1, R6.1, R7.1, R15.2, R29.2, R30.2, R31.2, R37.2, R38.2, R43.1, R44.2, R46.2, R52.2, R53.1, R74.1, R79.2, R83.1, R84.1, R90.1, R97.1, R98.1, R101.2, U1.4 (VCC), U2.1 (IN), U3.16 (VDRIVE), U4.1 (IN), U5.3 (VO), U8.12 (VDD), U9.21 (VDDIO), U10.12 (VDD), U11.8 (VCC), U12.1 (IN), U13.3 (VCC), U14.12 (VDD), U17.16 (VDRIVE), U19.21 (VDDIO), U20.1 (VCC_ONE), U20.9 (VCCIO1A), U20.31 (VCCIO2), U20.36 (VCC_ONE), U20.37 (VCC_ONE), U20.40 (VCCIO3), U20.49 (VCCIO3), U20.51 (VCC_ONE), U20.67 (VCCIO4), U20.72 (VCC_ONE), U20.73 (VCC_ONE), U20.94 (VCCIO6), U20.103 (VCCIO6), U20.108 (VCC_ONE), U20.109 (VCC_ONE), U20.115 (VCC_ONE), U20.128 (VCCIO8), U20.139 (VCCIO8), U20.144 (VCC_ONE), U22.3 (VCC), U23.1 (IN), U24.1 (IN), U24.3 (EN), X1.4 (Vdd), X2.1 (EN), X2.4 (Vdd)
+3.3VA: C91.1, C94.1, C97.1, C98.1, C100.1, C102.1, C104.1, C105.1, FB2.2, FB3.2, FB4.2, FB8.2, U20.2 (VCCA), U20.5 (ADC_VREF), U20.34 (VCCA), U20.35 (VCCA), U20.71 (VCCA), U20.107 (VCCA), U20.143 (VCCA)
+12V: C1.1, C2.1, C5.1, C6.1, C27.1, C33.1, C66.1, C83.1, D6.2 (A), PS1.2 (+Vin), R12.2, U5.1 (VI), U6.3 (VO), U7.2 (Vdd), U18.1 (VCC)
+BATT: C3.1, C4.1, C19.1, R25.1, SW3.2, TR1.3, U1.2 (VBAT), U6.1 (VI)
+VSW: C84.2, D9.1 (K), PS1.3 (-Vout), Q4.3 (S), R49.1, R102.2, U18.5 (VS), U18.6 (CS)
/+OUT: GD1.1, J4.1, L1.2, R24.2
/B+: BT1.1 (+), J9.1, SW3.1
/BINT: BT1.2 (-), BT2.1 (+)
/CVdiag: R30.1, U10.14 (DIAG)
/CVoutn: R62.1, U10.10 (OUTN)
/CVoutp: R61.1, U10.11 (OUTP)
/DisG: Q6.1 (G), R110.2
/HGNDCV: C50.2, C73.1, C74.2, C80.2, C81.2, R21.2, R28.1, U10.2 (DCDC_HGND), U10.7 (INN), U10.8 (HGND)
/HGNDLI: C45.2, C46.1, C47.2, C48.2, C49.2, FB7.1, U14.2 (DCDC_HGND), U14.8 (HGND)
/HGNDLV: C75.2, C76.1, C77.2, C78.2, C79.2, R81.2, R82.1, U8.2 (DCDC_HGND), U8.7 (INN), U8.8 (HGND)
/LIdiag: R52.1, U14.14 (DIAG)
/LIoutn: R40.1, U14.10 (OUTN)
/LIoutp: R39.1, U14.11 (OUTP)
/LSEN: GD1.3, L1.1, R102.1, R103.1
/LVdiag: R79.1, U8.14 (DIAG)
/LVoutn: R64.1, U8.10 (OUTN)
/LVoutp: R63.1, U8.11 (OUTP)
/SW: Q5.2 (D), R13.2, TR1.2, U1.6 (SW)
/VCCIO1B: C115.1, C116.1, J10.4, R75.1, R76.1, R78.1, R84.2, U20.23 (VCCIO1B)
/ain_1: R57.2, U20.14 (ADC1IN8)
/ain_2: R58.2, U20.13 (ADC1IN7)
/ain_3: R59.2, U20.12 (ADC1IN6)
/ain_4: R60.2, U20.11 (ADC1IN5)
/ain_5: R65.2, U20.10 (ADC1IN4)
/ain_6: R66.2, U20.8 (ADC1IN3)
/ain_7: R71.2, U20.7 (ADC1IN2)
/ain_8: R72.2, U20.6 (ADC1IN1)
/arm: R97.2, TP12.1, U20.120 (IO)
/arm_led: J1.25, J6.25, R11.2, U9.9 (GPIO18), U19.9 (GPIO18), U20.132 (IO)
/arm_led_oc: D2.1 (K), Q9.3 (C)
/bootsel: TP9.1, U20.126 (BOOTSEL)
/charge: J2.6, J3.6, R23.1, U9.20 (GPIO7), U19.20 (GPIO7), U20.62 (IO)
/conf_done: TP13.1, U20.138 (CONF_DONE)
/cont_led: J1.5, J6.5, R4.2, U9.23 (GPIO8), U19.23 (GPIO8), U20.135 (IO)
/cont_led_oc: D4.1 (K), Q10.3 (C)
/crc: TP15.1, U20.134 (CRC_ERR)
/cs: J1.21, J6.21, R17.1, R68.1, U9.7 (GPIO16), U19.7 (GPIO16), U20.106 (IO)
/dataA0: J1.13, J6.13, R18.1, U9.3 (GPIO12), U19.3 (GPIO12), U20.99 (IO)
/dataA1: J1.17, J6.17, R69.1, U9.5 (GPIO14), U19.5 (GPIO14), U20.102 (IO)
/dataB0: J1.15, J6.15, R19.1, U9.4 (GPIO13), U19.4 (GPIO13), U20.100 (IO)
/dataB1: J1.19, J6.19, R70.1, U9.6 (GPIO15), U19.6 (GPIO15), U20.105 (IO)
/devclrn: R88.2, TP11.1, U20.121 (DEVCLRN)
/devoe: TP10.1, U20.122 (DEVOE)
/dio0: J14.1, U20.118 (IO)
/dio1: J14.2, U20.119 (IO)
/dio2: J14.5, U20.113 (IO)
/dio3: J14.6, U20.114 (IO)
/dio4: J14.7, U20.111 (IO)
/dio5: J14.8, U20.112 (VREFB7N)
/dio6: J14.9, U20.110 (IO)
/done: R29.1, U1.8 (DONE)
/dump: J1.9, J6.9, R10.1, U9.1 (GPIO10), U19.1 (GPIO10), U20.66 (IO)
/gate: Q4.1 (G), R22.2
/hdmi_ck+: J12.10 (CK+), U20.52 (IO)
/hdmi_ck-: J12.12 (CK-), U20.50 (IO)
/hdmi_d0+: J12.7 (D0+), U20.56 (IO)
/hdmi_d0-: J12.9 (D0-), U20.55 (IO)
/hdmi_d1+: J12.4 (D1+), U20.58 (IO)
/hdmi_d1-: J12.6 (D1-), U20.57 (IO)
/hdmi_d2+: J12.1 (D2+), U20.60 (IO)
/hdmi_d2-: J12.3 (D2-), U20.59 (IO)
/iset0: R56.1, SW12.6, U20.127 (IO)
/iset1: SW12.5, U20.130 (IO)
/iset2: SW12.4, U20.131 (IO)
/jtagen: J10.8, R78.2, U20.15 (JTAGEN)
/launch_n: J1.7, J6.7, R50.1, R91.1, U9.24 (GPIO9), U19.24 (GPIO9), U20.124 (IO)
/mute_n: J2.18, J3.18, R54.1, R56.2, U9.14 (GPIO1), U19.14 (GPIO1)
/nstatus: TP7.1, U20.136 (NSTATUS)
/osc: J2.16, J3.16, R47.1, R86.1, U9.15 (GPIO2/refCLK), U19.15 (GPIO2/refCLK), U20.29 (CLK1P)
/pwm: J1.23, J6.23, R105.1, U9.8 (GPIO17), U19.8 (GPIO17), U20.65 (IO)
/pwmr: R9.2, R105.2, U18.2 (IN)
/reset_n: J2.24, J3.24, R48.1, R87.1, R88.1, U9.11 (nRST), U19.11 (nRST), U20.28 (CLK1N)
/sclk: J1.11, J6.11, R16.1, R67.1, U9.2 (GPIO11), U19.2 (GPIO11), U20.101 (IO)
/sleep_n: J2.26, U9.10 (nSLEEP), U19.10 (nSLEEP)
/speaker: J2.20, J3.20, R73.1, R108.1, U9.13 (GPIO0), U19.13 (GPIO0), U20.140 (IO)
/spi_ck: J2.14, J5.4, U9.16 (GPIO3/SPI_CK), U11.6 (SCK), U19.16 (GPIO3/SPI_CK)
/spi_clk: U20.87 (IO), U25.B2 (CK)
/spi_cs: U20.81 (IO), U25.A3 (nCS)
/spi_d0: U20.78 (IO), U25.D3 (DQ0)
/spi_d1: U20.85 (IO), U25.D2 (DQ1)
/spi_d2: U20.75 (IO), U25.C4 (DQ2)
/spi_d3: U20.77 (IO), U25.D4 (DQ3)
/spi_d4: U20.76 (IO), U25.D5 (DQ4)
/spi_d5: U20.79 (IO), U25.E3 (DQ5)
/spi_d6: U20.84 (IO), U25.E2 (DQ6)
/spi_d7: U20.86 (IO), U25.E1 (DQ7)
/spi_ds: U20.74 (IO), U25.C3 (RWDS)
/spi_nrst: U20.80 (VREFB5N), U25.A4 (nRST)
/spi_si: J2.10, J5.1, U9.18 (GPIO5/SPI_SI), U11.5 (MOSI), U19.18 (GPIO5/SPI_SI)
/spi_so: J2.8, J5.3, U9.19 (GPIO6/SPI_SO), U11.2 (MISO), U19.19 (GPIO6/SPI_SO)
/spi_ss: J2.12, J5.6, R44.1, R45.2, U9.17 (GPIO4/SPI_SS), U11.1 (~CS), U19.17 (GPIO4/SPI_SS)
/tck: J10.1, R77.1, U20.18 (TCK)
/tdi: J10.9, R75.2, U20.19 (TDI)
/tdo: J10.3, U20.20 (TDO)
/tms: J10.5, R76.2, U20.16 (TMS)
/vccio7: C141.1, C142.1, J14.4, R90.2, U20.117 (VCCIO7)
/vina0+: C55.1, R63.2, U3.1 (VINA+)
/vina0-: C57.1, R64.2, U3.2 (VINA-)
/vina1+: C38.1, R39.2, U17.1 (VINA+)
/vina1-: C39.1, R40.2, U17.2 (VINA-)
/vinb0+: C29.1, R35.2, U3.8 (VINB+)
/vinb0-: C30.1, R36.2, U3.7 (VINB-)
/vinb1+: C54.1, R61.2, U17.8 (VINB+)
/vinb1-: C56.1, R62.2, U17.7 (VINB-)
/vref0: C8.1, C9.1, U3.3 (REFA), U3.6 (REFB)
/vref1: C59.1, C60.1, U17.3 (REFA), U17.6 (REFB)
CVhi: R20.1, R99.1
CVlo: R21.1, R51.1
GND: BT2.2 (-), C1.2, C2.2, C3.2, C4.2, C5.2, C6.2, C7.2, C8.2, C9.2, C10.2, C11.2, C12.2, C13.2, C14.2, C15.2, C16.2, C17.2, C18.2, C19.2, C20.2, C21.2, C22.2, C23.2, C24.2, C25.2, C26.2, C27.2, C28.2, C29.2, C30.2, C32.2, C33.2, C34.2, C35.2, C36.2, C37.2, C38.2, C39.2, C40.2, C51.2, C52.2, C53.2, C54.2, C55.2, C56.2, C57.2, C58.2, C59.2, C60.2, C61.2, C62.2, C63.2, C64.2, C65.2, C66.2, C69.2, C70.2, C71.2, C82.2, C83.2, C90.2, C91.2, C92.2, C93.2, C94.2, C96.2, C97.2, C98.2, C99.2, C100.2, C101.2, C102.2, C103.2, C104.2, C105.2, C106.2, C108.2, C109.2, C110.2, C115.2, C116.2, C119.2, C120.2, C121.2, C122.2, C123.2, C124.2, C125.2, C126.2, C127.2, C128.2, C129.2, C130.2, C131.2, C132.2, C133.2, C134.2, C135.2, C136.2, C137.2, C139.2, C140.2, C141.2, C142.2, C143.2, C144.2, D9.2 (A), H1.1, H2.1, H3.1, H4.1, H9.1, J1.1, J1.2, J1.4, J1.6, J1.8, J1.10, J1.12, J1.14, J1.16, J1.18, J1.20, J1.22, J1.24, J1.26, J2.1, J2.2, J2.3, J2.5, J2.7, J2.9, J2.11, J2.13, J2.15, J2.17, J2.19, J2.21, J2.22, J2.23, J2.25, J3.1, J3.2, J3.3, J3.5, J3.7, J3.9, J3.11, J3.13, J3.15, J3.17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
LIhi: FB5.2, R49.2
LIlo: FB6.2, FB7.2, R103.2
LVhi: R24.1, R80.1
LVlo: R81.1, R104.1
unnamed: C31.1, R25.2, R27.2, R35.1
unnamed: C31.2, R26.2, R27.1, R36.1
unnamed: D2.2 (A), R15.1
unnamed: D3.1 (K), R57.1
unnamed: D4.2 (A), R31.1
unnamed: D5.1, TR1.4
unnamed: C17.1, D6.1 (K), Q1.2 (S)
unnamed: D7.2 (A), Q2.3 (C), R12.1
unnamed: D7.1 (K), Q1.1 (G), R1.2
unnamed: D8.1 (K), R58.1
unnamed: D10.1 (K), R59.1
unnamed: D11.1 (K), R60.1
unnamed: D12.1 (K), R65.1
unnamed: D13.1 (K), R66.1
unnamed: D14.1 (K), R71.1
unnamed: D15.1 (K), R72.1
unnamed: FB5.1, R33.1
unnamed: C84.1, PS1.4 (+Vout), U18.8 (VB)
unnamed: Q1.3 (D), R2.2, R110.1
unnamed: Q2.2 (B), R10.2
unnamed: Q3.1 (B), R108.2
unnamed: D1.1 (K), LS1.2, Q3.3 (C)
unnamed: Q5.1 (G), R5.2
unnamed: Q7.1 (B), R73.2
unnamed: D16.1 (K), LS2.2, Q7.3 (C)
unnamed: Q9.1 (B), R11.1
unnamed: Q10.1 (B), R4.1
unnamed: R32.2, R55.1, TR1.1
unnamed: R50.2, R83.2, SW10.2
unnamed: R74.2, R91.2, SW2.2
unnamed: R53.2, R54.2, SW1.2 (B)
unnamed: R14.2, R23.2, U1.9 (CHRG), U7.3 (IN)
unnamed: C40.1, U1.10 (CT)
unnamed: R13.1, U1.3 (RFB)
unnamed: R8.1, U1.1 (RREF)
unnamed: R55.2, U1.7 (SEC)
unnamed: R7.2, U2.3 (EN)
unnamed: R16.2, U3.15 (SCLK)
unnamed: R18.2, U3.14 (SDATAA)
unnamed: R19.2, U3.13 (SDATAB)
unnamed: R17.2, U3.10 (nCS)
unnamed: R6.2, U4.3 (EN)
unnamed: R5.1, U7.5 (OUT)
unnamed: C69.1, U8.13 (LDO_OUT), U8.16 (DCDC_IN)
unnamed: C75.1, C76.2, C78.1, U8.1 (DCDC_OUT), U8.3 (HLDO_IN)
unnamed: C77.1, C79.1, U8.5 (HLDO_OUT)
unnamed: R80.2, R82.2, U8.6 (INP)
unnamed: C82.1, U10.13 (LDO_OUT), U10.16 (DCDC_IN)
unnamed: C50.1, C73.2, C80.1, U10.1 (DCDC_OUT), U10.3 (HLDO_IN)
unnamed: C74.1, C81.1, U10.5 (HLDO_OUT)
unnamed: R20.2, R28.2, U10.6 (INP)
unnamed: R37.1, R42.2, U11.7 (~HOLD)
unnamed: R38.1, R41.2, U11.3 (~WP)
unnamed: R43.2, U12.3 (EN)
unnamed: R48.2, U13.2 (~RESET)
unnamed: C53.1, U14.13 (LDO_OUT), U14.16 (DCDC_IN)
unnamed: C45.1, C46.2, C48.1, U14.1 (DCDC_OUT), U14.3 (HLDO_IN)
unnamed: C47.1, C49.1, U14.5 (HLDO_OUT)
unnamed: C44.1, R33.2, U14.6 (INP)
unnamed: R67.2, U17.15 (SCLK)
unnamed: R69.2, U17.14 (SDATAA)
unnamed: R70.2, U17.13 (SDATAB)
unnamed: R68.2, U17.10 (nCS)
unnamed: R22.1, U18.7 (HO)
unnamed: R101.1, U20.129 (NCONFIG)
unnamed: R87.2, U22.2 (~RESET)
unnamed: R98.2, U23.3 (EN)
unnamed: R46.1, X1.1 (EN)
unnamed: R47.2, X1.3 (OUT)
unnamed: R86.2, X2.3 (OUT)

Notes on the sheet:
2x HDMI Video Out
600V
Evaluation Probe
Power-off Discharge
Igniter
Capacitor Voltage
Energy Storage and Control
*done*
41x gain
Coil
Capacitor Voltage Sense 1V/401V
High Voltage Control
Output Voltage
Ishunt
Output Voltage Sense 1V/401V
Instrumentation
CAP
Emulator Connector
32MB Capture Buffer Octal xSPI 400 MB/s
Launch Control Chip
2.0x gain
XS LCC
25V
FPGA Config
Front Panel
IC Charger
4x 3msps 12bit ADC Interface
Development Support (Optional)
ALT XS
Analog Expansion
FPGA Power
Emulation and Monitor Probe
Discharge Energy Sink Resistor
Digital I/O
*clk+*
Clock & Reset
*tx*
60V 3A
Power Supply
*clk-*

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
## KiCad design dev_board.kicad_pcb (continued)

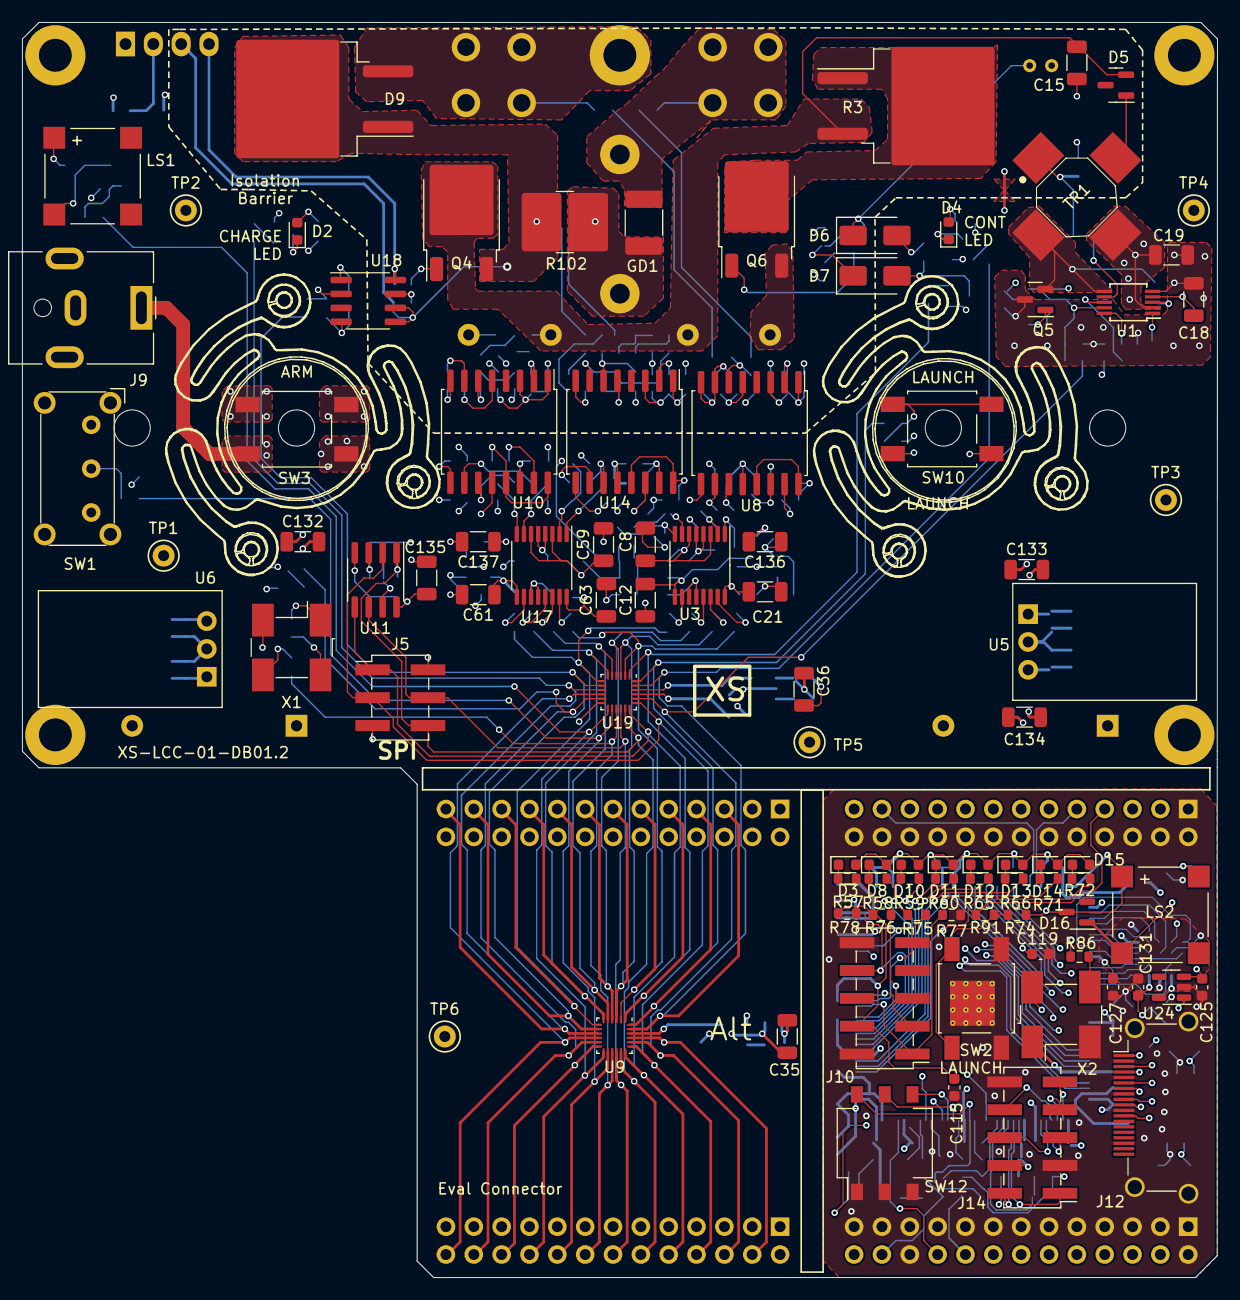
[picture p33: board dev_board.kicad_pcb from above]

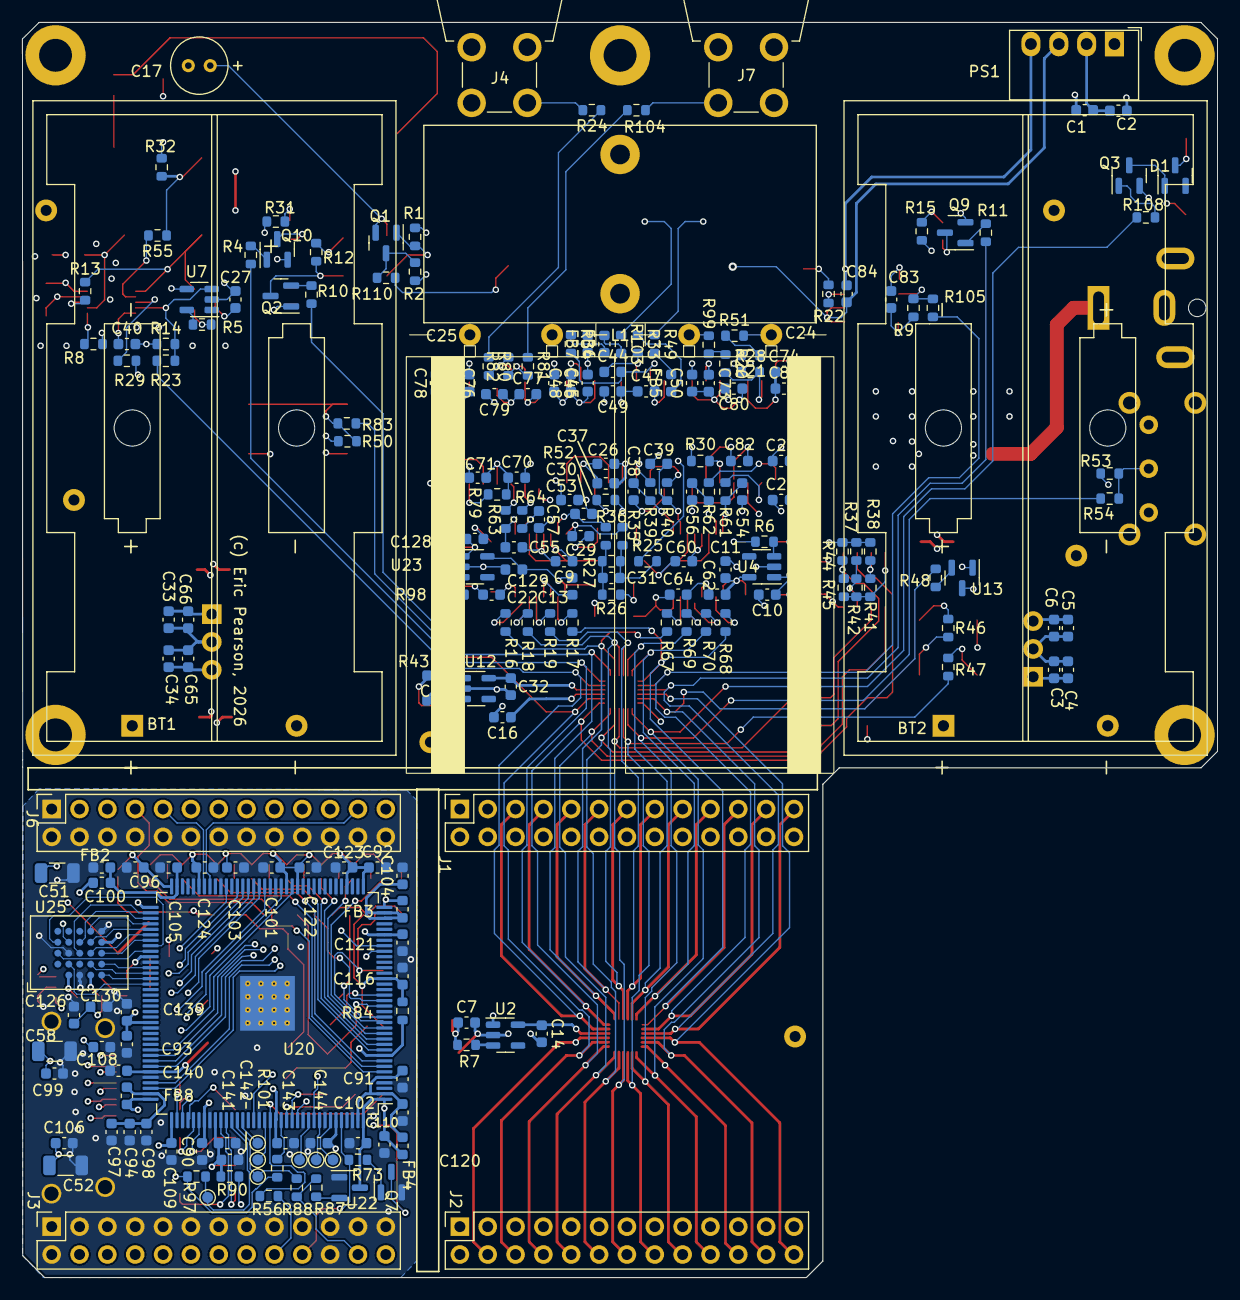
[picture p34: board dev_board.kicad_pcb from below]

Board: 6 copper layers, 109.0 x 114.5 mm, 323 parts (224 on the bottom side), 195 nets.

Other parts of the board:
R3: 3K3 25W; TO-263-2_TabPin1

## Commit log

2025-10-02 Add Eval board slide picture, value, features
2025-10-02 Update README.md with evaluation board slide
2025-10-06 update eval board features and photo
2025-10-18 add eval board circuit examples
2025-10-18 Add minimum viable circuit for EB
2025-10-21 5 wire launch cable
2026-02-05 LCC Dev Board v0.1 KiCad project, schematic and pcb
    [dev_board.kicad_pcb, dev_board.kicad_sch]
2026-02-05 Added Dev Board development notes
2026-02-09 Closer to tapeout, Digikey BOM added
    [dev_board.csv, dev_board.kicad_pcb, dev_board.kicad_sch]
2026-02-10 Added PCB links
    Updated sections for clarity and added links to KiCAD files.
2026-02-21 prelim dev board
2026-02-21 dev board slide README
2026-02-23 Tapeout v01.2
    [dev_board.csv, dev_board.kicad_pcb, dev_board.kicad_sch]
2026-02-23 Updated dev board slide to match v1.2 pcb tapeout
2026-05-10 LCC-XB experimental engineering 24 pin DIP module draft v0.1
    [eng_board.kicad_pcb, eng_board.kicad_sch]
2026-05-10 Add datasheet page for LCC engineering experimental PCB (24pin DIP module)
2026-05-12 change back to dual ADCs (with internal refs) for now. Leave the low cost ADCs to the future
    [eng_board.kicad_pcb, eng_board.kicad_sch]
2026-05-24 MVP enclosure parts
    [button.stp.stl, lcc button ring v1_1.stl, lcc coil cov v1_5.stl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]
2026-05-24 Update README with prototype launch controller details
    Added information about extra prototype devices for sale.
2026-05-26 Add psb tapeout gerbers
2026-05-26 Add dev board PCB ECO notes text file.
